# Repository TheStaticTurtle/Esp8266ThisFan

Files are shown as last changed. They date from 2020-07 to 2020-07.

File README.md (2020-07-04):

# Esp8266ThisFan

### PCB + SCHEMATICS Are outdated see my mistakes in the blog post

This is a project where I convert a plain old desk fan into a wireless enabled beast for home automatisation. Link to the blog post [blog.thestaticturtle.fr/hacking-the-hardware-store-fan/](blog.thestaticturtle.fr/hacking-the-hardware-store-fan/)

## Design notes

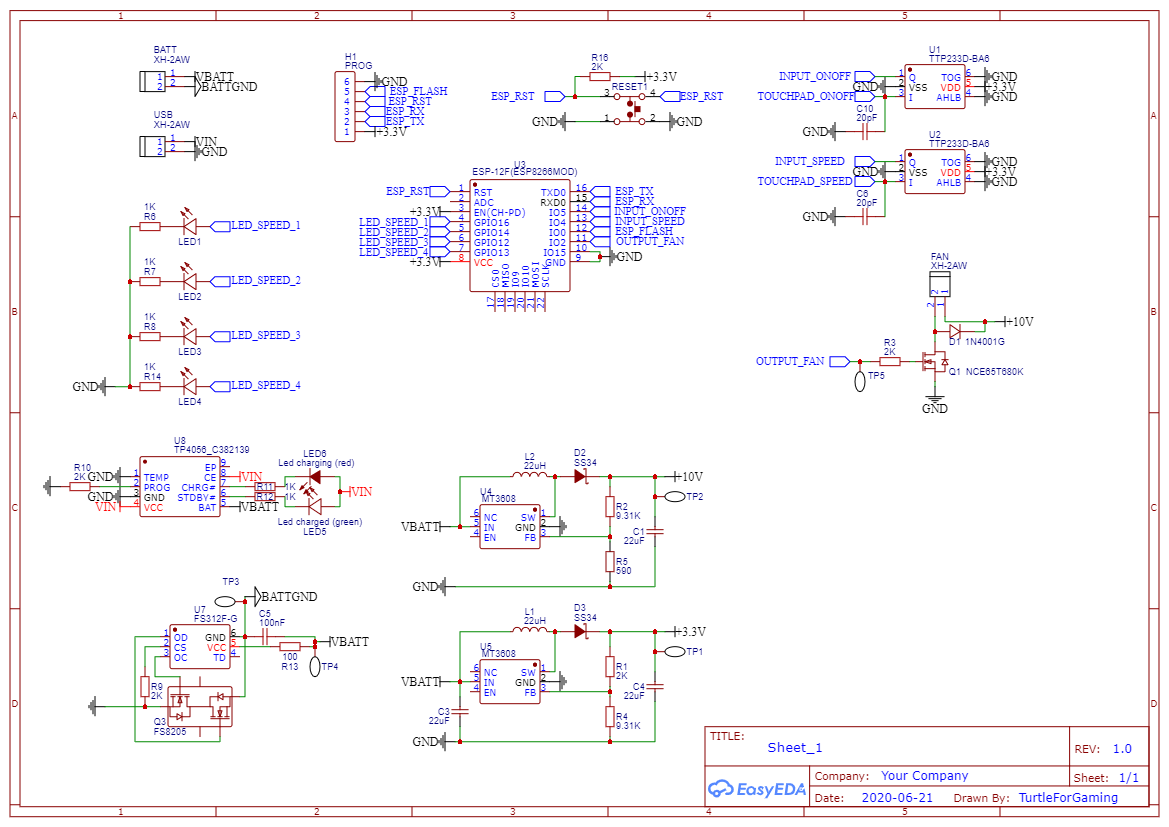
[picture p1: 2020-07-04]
hardware/schematic/Schematic_esp8266-ed_fan_2020-07-05_01-04-33.png

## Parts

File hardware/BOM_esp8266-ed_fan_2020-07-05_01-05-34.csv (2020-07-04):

ID | Name | Designator | Footprint | Quantity | Manufacturer Part | Manufacturer | Supplier | Supplier Part | LCSC Assembly
1 | FS8205 | Q3 | SOT-23-6 | 1 | FS8205 | FORTUNE | LCSC | C32254
2 | MT3608 | U5,U4 | SOT-23-6 | 2 | MT3608 | LCSC | LCSC | C84817
3 | 22uH | L1,L2 | 7*7*4 | 2 | SMRH74-220MT | LCSC | LCSC | C27442
4 | SS34 | D3,D2 | SMA(DO-214AC) | 2 | SS34 |  | LCSC | C8678
5 | 22uF | C3,C4,C1 | 1812 | 3 | 1812X226K250NT | FH | LCSC | C28504
6 | FS312F-G | U7 | SOT-23-6_L2.9-W1.6-P0.95-LS2.8-BR | 1 | FS312F-G | FORTUNE | LCSC | C82736 | Yes
7 | TTP233D-BA6 | U1,U2 | SOT-23-6_L2.9-W1.6-P0.95-LS2.8-BR | 2 | TTP233D-BA6 | TONTEK | LCSC | C82384 | Yes
8 | 1K | R11,R12,R6,R7,R8,R14 | R0805 | 6 | CR0805J80102G | LIZ Elec | LCSC | C328385
9 | 9.31K | R4,R2 | R0805 | 2 | RMC08059.31K1%N | Tyohm | LCSC | C325873
10 | 100nF | C5 | C0805 | 1 | GRM21BR72A104KAC4L | MuRata | LCSC | C86044
11 | NCE65T680K | Q1 | TO-252-2_L6.6-W6.1-P4.57-LS9.9-BR-CW | 1 | NCE65T680K | Wuxi NCE Power Semiconductor | LCSC | C216787
12 | PROG | H1 | HDR-TH_6P-P2.54-V | 1 | Header-Male-2.54_1x6 | BOOMELE | LCSC | C37208
13 | Led charging (red) | LED6 | LED1206-R-RD | 1 |  |  | LCSC | C192318
14 | 2K | R9,R10,R1,R3,R16 | R0805 | 5 | CR0805-FX-2001ELF | BOURNS | LCSC | C203834
15 | XH-2AW | BATT,USB,FAN | CONN-TH_2P-P2.50_XH-2AW | 3 | XH-2AW | BOOMELE | LCSC | C33132
16 | TP4056_C382139 | U8 | ESOP-8_L4.9-W3.9-P1.27-LS6.0-BL-EP | 1 | TP4056 | TPOWER | LCSC | C382139 | Yes
17 | Led charged (green) | LED5,LED1,LED2,LED3,LED4 | LED1206-RD | 5 |  |  | LCSC | C192319
18 | RESET | RESET1 | TACTILE SWITCH THT 6X6MM | 1 |  |  | LCSC | C393938
19 | 100 | R13 | R0805 | 1 | 080500F1000T5E | UniOhm | LCSC | C146168
20 | ESP-12F(ESP8266MOD) | U3 | WIFIM-SMD_ESP-12F-ESP8266MOD | 1 | ESP-12F(ESP8266MOD) | Ai-Thinker | LCSC | C82891
21 | 20pF | C10,C6 | C0603 | 2 | 0603N200J500 | Walsin Tech Corp | LCSC | C123543
22 | 1N4001G | D1 | SMA_L4.4-W2.6-LS5.0-RD | 1 | 1N4001G | Shikues | LCSC | C433392
23 | TEST_PAD | TP1,TP2,TP3,TP4,TP5 | TESTPAD0 | 5 | TESTPAD
24 | 590 | R5 | R0805 | 1 | CR0805F85900G | LIZ | LCSC | C101801

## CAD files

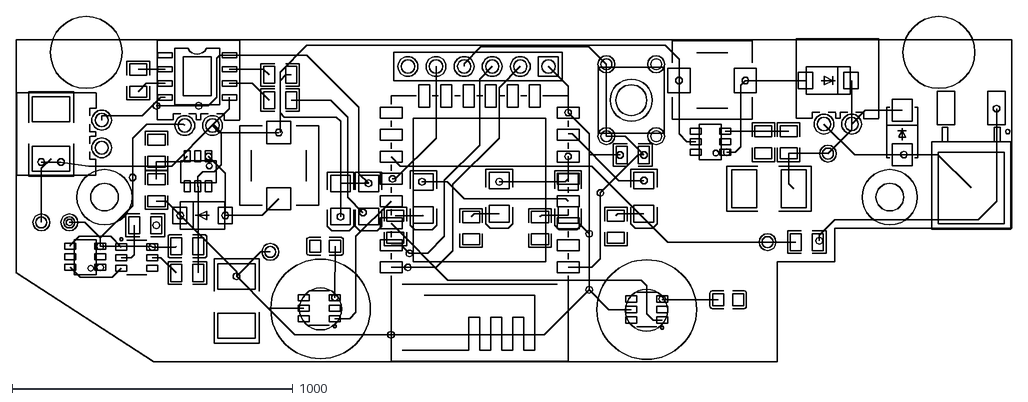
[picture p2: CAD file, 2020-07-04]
hardware/pcb/PCB_2020-06-22_00-26-27_2020-07-05_01-06-46.dxf
3545.0 x 1228.0

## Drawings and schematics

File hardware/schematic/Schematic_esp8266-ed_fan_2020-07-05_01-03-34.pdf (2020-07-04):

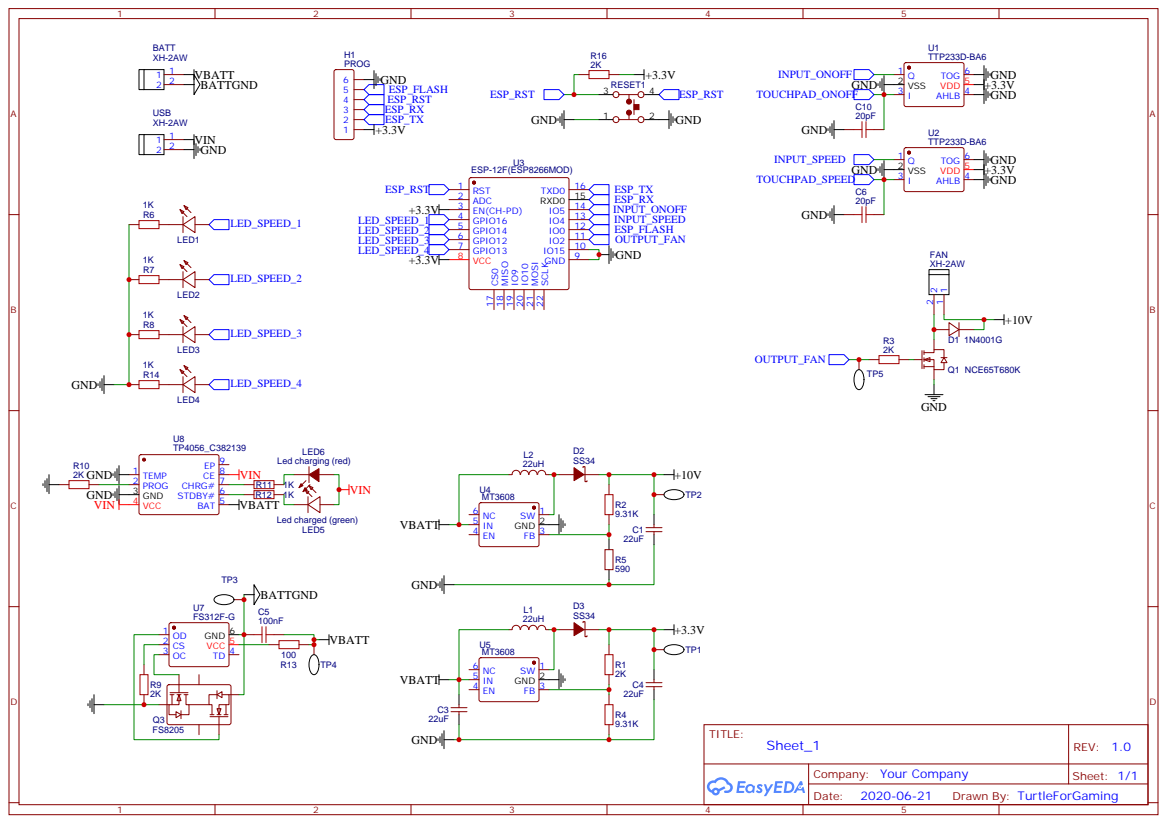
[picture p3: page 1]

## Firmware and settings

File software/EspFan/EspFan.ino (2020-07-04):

#include <ESP8266WiFi.h>
#include <ESP8266mDNS.h>
#include <WiFiUdp.h>
#include <ArduinoOTA.h>
#include <PubSubClient.h>

const int IO_INPUT_SPEED   = D1;
const int IO_INPUT_ONOFF   = D2;
const int IO_OUTPUT_SPEED1 = D7;
const int IO_OUTPUT_SPEED2 = D6;
const int IO_OUTPUT_SPEED3 = D5;
const int IO_OUTPUT_SPEED4 = D0;
const int IO_OUTPUT_FAN    = D4;

#ifndef STASSID
#define STASSID "------------"
#define STAPSK  "------------"
#endif

const char* ssid = STASSID;
const char* password = STAPSK;
const char* mqtt_server = "------------";
const char* mqtt_user = "------------";
const char* mqtt_pass = "------------";

const char* mqtt_state             = "/iot/fan/1/state";
const char* mqtt_command           = "/iot/fan/1/set";
const char* mqtt_speed_state       = "/iot/fan/1/speed/state";
const char* mqtt_speed_command     = "/iot/fan/1/speed/set";
const char* mqtt_speed_state_raw   = "/iot/fan/1/speed/state_raw";
//const char* mqtt_speed_command_raw = "/iot/fan/1/speed/set_raw";

int  fanSpeed = 0;
bool isFanRunning = false;

WiFiClient espClient;
PubSubClient client(espClient);

void writePercentageToLeds(int percentage, bool forceDisplay) {
  digitalWrite(IO_OUTPUT_SPEED1, percentage >  0   && (isFanRunning || forceDisplay));
  digitalWrite(IO_OUTPUT_SPEED2, percentage >= 50  && (isFanRunning || forceDisplay));
  digitalWrite(IO_OUTPUT_SPEED3, percentage >= 75  && (isFanRunning || forceDisplay));
  digitalWrite(IO_OUTPUT_SPEED4, percentage == 100 && (isFanRunning || forceDisplay));
}

void setFanSpeed(int speed) {
  if(speed == 0) {
    digitalWrite(IO_OUTPUT_FAN,LOW);
  } else {
    analogWriteFreq(15);
    analogWrite(IO_OUTPUT_FAN, map(speed,0,100,275,1023));
  }
}

void sendToMqtt() {
  if(!client.connected()) { return;}
  if(isFanRunning) {
    client.publish(mqtt_state, "ON");
  } else {
    client.publish(mqtt_state, "OFF");
  }
  if(fanSpeed == 100) {
    //client.publish(mqtt_speed_state, "ON"); //Homeassistant don't suport 4 states
    client.publish(mqtt_speed_state, "HIGH");
  } else if(fanSpeed >= 75) {
    client.publish(mqtt_speed_state, "HIGH");
  } else if(fanSpeed >= 50) {
    client.publish(mqtt_speed_state, "MEDIUM");
  } else if(fanSpeed > 0) {
    client.publish(mqtt_speed_state, "LOW");
  } else {
    client.publish(mqtt_speed_state, "OFF");
  }
  
  client.publish(mqtt_speed_state_raw, String(fanSpeed).c_str());
}



void mqtt_callback(char* topic, byte* payload, unsigned int length) {
  Serial.print("Message arrived [");
  Serial.print(topic);
  Serial.print("] ");
  for (int i = 0; i < length; i++) {
    Serial.print((char)payload[i]);
  }
  Serial.println();
  
  if (strcmp(topic,mqtt_command)==0) {
    if (String((char*)payload).startsWith("ON"))  { fanSpeed=25;  isFanRunning = true;  }
    if (String((char*)payload).startsWith("OFF")) { fanSpeed=0;   isFanRunning = false; }
  } 
  else if (strcmp(topic,mqtt_speed_command)==0){
    if (String((char*)payload).startsWith("ON"))     { fanSpeed=100; isFanRunning = true;  }
    if (String((char*)payload).startsWith("HIGH"))   { fanSpeed=75;  isFanRunning = true;  }
    if (String((char*)payload).startsWith("MEDIUM")) { fanSpeed=50;  isFanRunning = true;  }
    if (String((char*)payload).startsWith("LOW"))    { fanSpeed=25;  isFanRunning = true;  }
    if (String((char*)payload).startsWith("OFF"))    { fanSpeed=0;   isFanRunning = false; }
  }
  
  /*if (strcmp(topic,mqtt_speed_command_raw)==0)
  
  }*/
  setFanSpeed(fanSpeed);
  sendToMqtt();
}

void mqtt_reconnect() {
  while (!client.connected()) {
    writePercentageToLeds(100,true);
    delay(50);
    writePercentageToLeds(0,true);
    delay(50);
    
    Serial.print("Attempting MQTT connection...");
    String clientId = "EspFan-01-";
    clientId += String(random(0xffff), HEX);
    if (client.connect(clientId.c_str(),mqtt_user,mqtt_pass)) {
      Serial.println("Connected to mqtt server");
      client.subscribe(mqtt_command);
      client.subscribe(mqtt_speed_command);
      sendToMqtt();
    } else {
      Serial.print("failed, rc=");
      Serial.print(client.state());
      Serial.println(" try again in 5 seconds");
      delay(1000);
    }
  }
}


void setup() {
  // initialize digital pin LED_BUILTIN as an output.
  pinMode(IO_INPUT_SPEED  , INPUT);
  pinMode(IO_INPUT_ONOFF  , INPUT);
  pinMode(IO_OUTPUT_SPEED1, OUTPUT);
  pinMode(IO_OUTPUT_SPEED2, OUTPUT);
  pinMode(IO_OUTPUT_SPEED3, OUTPUT);
  pinMode(IO_OUTPUT_SPEED4, OUTPUT);
  pinMode(IO_OUTPUT_FAN   , OUTPUT);
  digitalWrite(IO_OUTPUT_SPEED1, LOW);
  digitalWrite(IO_OUTPUT_SPEED2, LOW);
  digitalWrite(IO_OUTPUT_SPEED3, LOW);
  digitalWrite(IO_OUTPUT_SPEED4, LOW);
  digitalWrite(IO_OUTPUT_FAN   , LOW);
  pinMode(D1, INPUT);


  Serial.begin(115200);
  Serial.println("Booting");
  
  WiFi.mode(WIFI_STA);
  WiFi.begin(ssid, password);

  ArduinoOTA.setHostname("EspFan-01");
  ArduinoOTA.onStart([]() {
    Serial.println("Start update");
    writePercentageToLeds(0,true);
  });
  ArduinoOTA.onEnd([]() {
    for(int i=0; i<10; i++) {
      writePercentageToLeds(100,true);
      delay(50);
      writePercentageToLeds(0,true);
      delay(50);
    }
  });
  ArduinoOTA.onProgress([](unsigned int progress, unsigned int total) {
    writePercentageToLeds((progress / (total / 100)),true);
    Serial.printf("Progress: %u%%\r", (progress / (total / 100)));
  });
  ArduinoOTA.onError([](ota_error_t error) {
    Serial.printf("Error[%u]: ", error);
    if (error == OTA_AUTH_ERROR) {
      Serial.println("Auth Failed");
    } else if (error == OTA_BEGIN_ERROR) {
      Serial.println("Begin Failed");
    } else if (error == OTA_CONNECT_ERROR) {
      Serial.println("Connect Failed");
    } else if (error == OTA_RECEIVE_ERROR) {
      Serial.println("Receive Failed");
    } else if (error == OTA_END_ERROR) {
      Serial.println("End Failed");
    }
  });
  ArduinoOTA.begin();
    
  writePercentageToLeds(0,true);

  
  client.setServer(mqtt_server, 1883);
  client.setCallback(mqtt_callback);
}


void loop() {

  if (WiFi.status() != WL_CONNECTED) { // Wait for the Wi-Fi to connect
    writePercentageToLeds(100,true);
    delay(50);
    writePercentageToLeds(0,true);
    delay(50);
  } else {
    ArduinoOTA.handle();
    if (!client.connected()) {
      mqtt_reconnect();
    }
    client.loop();
    writePercentageToLeds(fanSpeed,false);
  }
  
  if(digitalRead(IO_INPUT_SPEED) && isFanRunning) {
    fanSpeed += 25;
    if(fanSpeed >100) { fanSpeed = 25; }
    setFanSpeed(fanSpeed);
    writePercentageToLeds(fanSpeed,false);
    sendToMqtt();
    while(digitalRead(IO_INPUT_SPEED)) {}
    delay(10);
  }
  if(digitalRead(IO_INPUT_ONOFF)) {
    isFanRunning = !isFanRunning;
    fanSpeed = isFanRunning ? 25 :0;
    setFanSpeed(fanSpeed);
    writePercentageToLeds(fanSpeed,false);
    sendToMqtt();
    while(digitalRead(IO_INPUT_ONOFF)) {}
    delay(10);
  }
}

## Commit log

2020-07-04 Added arduino code
2020-07-04 Added hardware
    [ALTIUM_2020-06-22_00-26-27_2020-07-05_01-07-09.pcbdoc, ALTIUM_Sheet_1_2020-07-05_01-04-44.schdoc, BOM_esp8266-ed_fan_2020-07-05_01-05-34.csv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]
